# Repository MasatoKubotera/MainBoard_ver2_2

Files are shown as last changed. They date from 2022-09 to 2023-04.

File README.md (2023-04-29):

<html lang="en">
  <head>
    <meta charset="uft-8">
    <meta name="author" content="Masato Kubotera">
  </head>
  <body>
    <h1>Main Board Ver. 2.2</h1>
    <h2>About Main Board</h2>
    <p>
      The Main Board is a single board that integrates the circuits for driving the robot designed to be mounted on SUSTAINA-OP.
      <br>
      <br>
      Note that this is Ver. 2.2. For other versions, please refer to the following repositories.
      <ul>
        <li><a href="https://github.com/MasatoKubotera/MainBoard_ver2_0">Main Board Ver. 2.0</a></li>
        <li><a href="https://github.com/MasatoKubotera/MainBoard_ver2_1">Main Board Ver. 2.1</a></li>
      </ul>
      <h2>About Ver. 2.2</h2>
      now writing...
      <br><br>
      It is actually used for the 6th generation robot SUSTAINA-OP of the RoboCup Humanoid League team CIT Brains competed in the RoboCup 2022.<br><br>
      <!--
      -->
      <table>
        <tr>
          <td>
            <a href="image/brd_top.png">
              <div align="center">
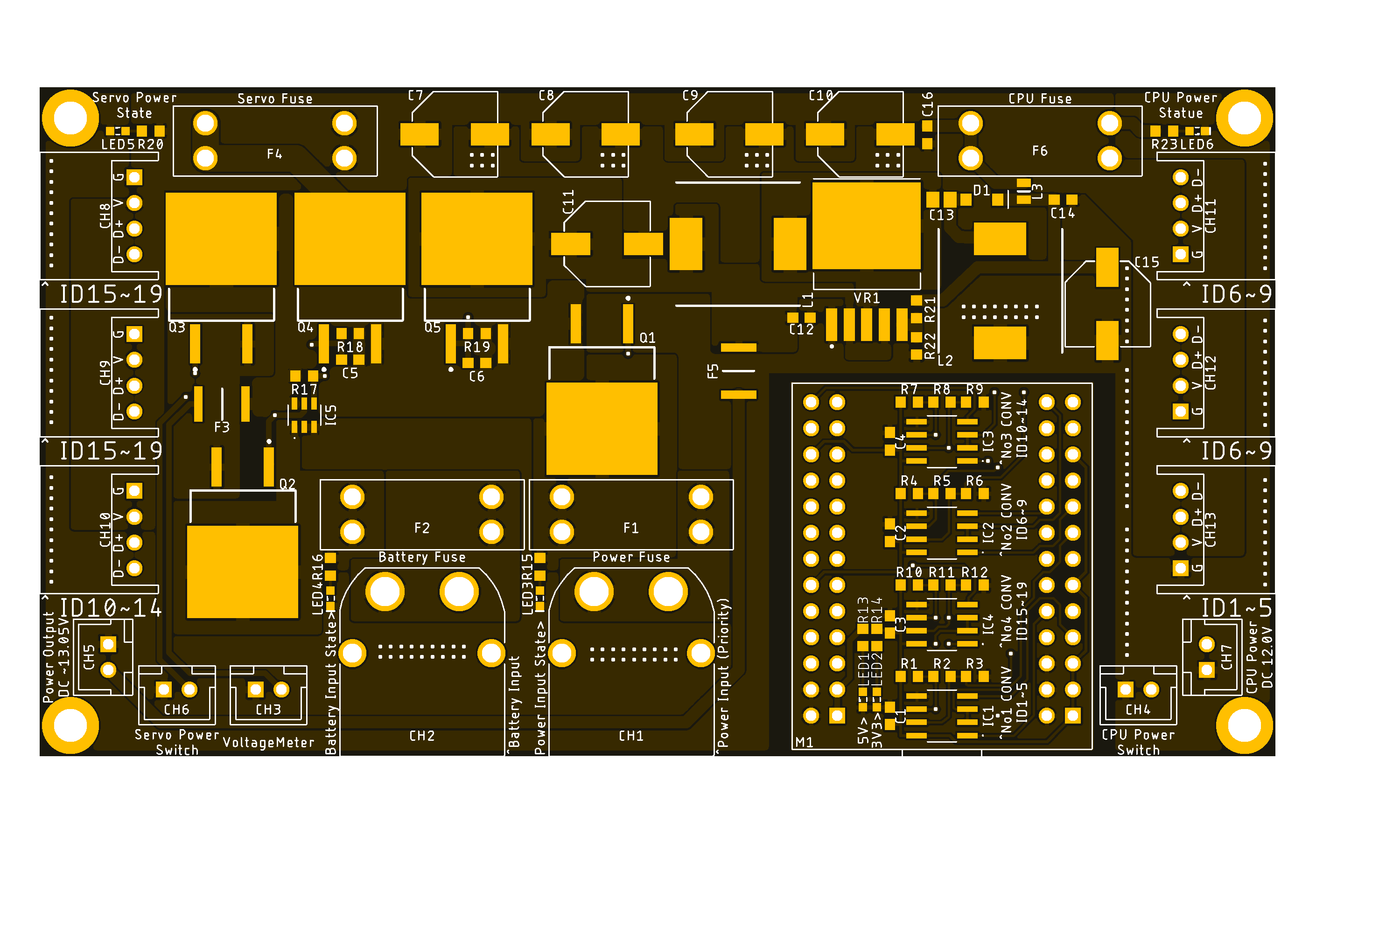
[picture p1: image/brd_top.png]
                
              </div>
            </a>
          </td>
          <td>
            <div align="center">
              
            </div>
          </td>
          <td>
            <div align="center">
              
            </div>
          </td>
        </tr>
        <tr>
          <td>
            <div align="center">
              PCB preview image
            </div>
          </td>
          <td>
            <div align="center">
              After mounting electronic components
            </div>
          </td>
          <td>
            <div align="center">
              After attaching module board
            </div>
          </td>     
        </tr>
      </table>
    </p>
    <h2>Repository Contents</h2>
    <p>
    <dl>
      <dt>\image</dt>
      <dd>PCB preview images and capture of design screen</dd>
      <dt>\libraries</dt>
      <dd>Libraries used in Autodesk Eagle design</dd>
      <dt>Schematic.pdf</dt>
      <dd>Circuit diagram of this product</dd>
      <dt>BOM.txt</dt>
      <dd>Parts lists output from design data</dd>
      <dt>.brd</dt>
      <dd>Board wiring design file by Autodesk Eagle</dd>
      <dt>.sch</dt>
      <dd>Schematic design file by Autodesk Eagle</dd>
      <dt>Gerber_data.zip</dt>
      <dd>Zip folder of Gerber format files for PCB manufacturing requests.</dd>
      <dt>LICENSE</dt>
      <dd>This is a license to use this product. Please confirm before use.</dd>
      <dt>.gitignore</dt>
      <dd>File to exclude cache files from management.</dd>
    </dl>
    </p>
    <h2>Documentation</h2>
      <p>
        <h3>BOM</h3>
        The BOM below shows the components actually mounted on the SUSTAINA-OP equipped MainBoard in RoboCup2022. Many of these boards have been created, and in some cases substitutes have been used. Their details are listed below the BOM.
          <table>
            <thead>
              <tr>
                <th> Eagle Design Parts # </th>
                <th> Q'ty </th>
                <th> Mfr. Product # </th>
                <th> Supplier </th>
                <th> Description </th>
              </tr>
            </thead>
            <tbody>
              <tr>
                <td>C1, C2, C3, C4, C5, C6</td>
                <td>6</td>
                <td>C1608JB1H104K</td>
                <td><a href="https://akizukidenshi.com/catalog/g/gP-06166/">Akizuki</a></td>
                <td>Multilayer Ceramic Capacitors SMD/SMT 0.1uF 50V 10% 0603</td>
              </tr>
              <tr>
                <td>C11,C15</td>
                <td>2</td>
                <td>UWT1E221MNL1GS</td>
                <td><a href="https://akizukidenshi.com/catalog/g/gP-10420/">Akizuki</a></td>
                <td>Aluminum Electrolytic Capacitors SMD/SMT 220uF 25V 20% AEC-Q200</td>
              </tr>
              <tr>
                <td>C12,C14</td>
                <td>2</td>
                <td>GRM188R71E105KA12</td>
                <td><a href="https://akizukidenshi.com/catalog/g/gP-14526/">Akizuki</a></td>
                <td>Multilayer Ceramic Capacitors SMD/SMT 1uF 25V 10% 0603</td>
              </tr>
              <tr>
                <td>C13</td>
                <td>1</td>
                <td>GRM21BR61E226ME44</td>
                <td><a href="https://akizukidenshi.com/catalog/g/gP-08240/">Akizuki</a></td>
                <td>Multilayer Ceramic Capacitors SMD/SMT 22uF 25V 15% 0603</td>
              </tr>
              <tr>
                <td>C16</td>
                <td>1</td>
                <td>GRM188R6YA106MA73</td>
                <td><a href="https://akizukidenshi.com/catalog/g/gP-13161/">Akizuki</a></td>
                <td>Multilayer Ceramic Capacitors SMD/SMT 10uF 35V 20% 0603</td>
              </tr>
              <tr>
                <td>C7, C8, C9, C10</td>
                <td>4</td>
                <td>35PFV150M8X10.5</td>
                <td><a href="https://akizukidenshi.com/catalog/g/gP-14492/">Akizuki</a></td>
                <td>Aluminum Organic Polymer Capacitors SMD/SMT 150uF 35V 20% AEC-Q200</td>
              </tr>
              <tr>
                <td>CH1, CH2</td>
                <td>2</td>
                <td>XT60PW-M</td>
                <td><a href="https://store.shopping.yahoo.co.jp/suzakulab/amass-xt60pw-m.html">Suzaku Lab.</a></td>
                <td>DC Power Connector, Through Hole, Horizontal, Male, 30A 500V</td>
              </tr>
              <tr>
                <td>CH3</td>
                <td>1</td>
                <td>B2B-XH-A-BLACK</td>
                <td><a href="https://www.daisen-netstore.com/shopdetail/000000000029/ct15/page1/order/">DAISEN</a></td>
                <td>Connector Header Through Hole, Top entry 2 position 2.54mm BLACK</td>
              </tr>
              <tr>
                <td>CH4</td>
                <td>1</td>
                <td>B2B-XH-A-BLUE</td>
                <td><a href="https://www.daisen-netstore.com/shopdetail/000000000029/ct15/page1/order/">DAISEN</a></td>
                <td>Connector Header Through Hole, Top entry 2 position 2.54mm BLUE</td>
              </tr>
              <tr>
                <td>CH5</td>
                <td>1</td>
                <td>B2B-XH-A-GREEN</td>
                <td><a href="https://www.daisen-netstore.com/shopdetail/000000000029/ct15/page1/order/">DAISEN</a></td>
                <td>Connector Header Through Hole, Top entry 2 position 2.54mm GREEN</td>
              </tr>
              <tr>
                <td>CH6</td>
                <td>1</td>
                <td>B2B-XH-A-YELLOW</td>
                <td><a href="https://www.daisen-netstore.com/shopdetail/000000000029/ct15/page1/order/">DAISEN</a></td>
                <td>Connector Header Through Hole, Top entry 2 position 2.54mm YELLOW</td>
              </tr>
              <tr>
                <td>CH7</td>
                <td>1</td>
                <td>B2B-XH-A-RED</td>
                <td><a href="https://www.daisen-netstore.com/shopdetail/000000000029/ct15/page1/order/">DAISEN</a></td>
                <td>Connector Header Through Hole, Top entry 2 position 2.54mm RED</td>
              </tr>
              <tr>
                <td>CH8, CH9</td>
                <td>2</td>
                <td>S4B-XH-A(LF)(SN)-YELLOW</td>
                <td><a href="https://www.daisen-netstore.com/shopdetail/000000000028/ct15/page1/order/">DAISEN</a></td>
                <td>Connector Header Through Hole, Side entry 4 position 2.54mm YELLOW</td>
              </tr>
              <tr>
                <td>CH10</td>
                <td>1</td>
                <td>S4B-XH-A(LF)(SN)-GREEN</td>
                <td><a href="https://www.daisen-netstore.com/shopdetail/000000000028/ct15/page1/order/">DAISEN</a></td>
                <td>Connector Header Through Hole, Side entry 4 position 2.54mm GREEN</td>
              </tr>
              <tr>
                <td>CH11, CH12</td>
                <td>2</td>
                <td>S4B-XH-A(LF)(SN)-BLUE</td>
                <td><a href="https://www.daisen-netstore.com/shopdetail/000000000028/ct15/page1/order/">DAISEN</a></td>
                <td>Connector Header Through Hole, Side entry 4 position 2.54mm BLUE</td>
              </tr>
              <tr>
                <td>CH13</td>
                <td>1</td>
                <td>S4B-XH-A(LF)(SN)-RED</td>
                <td><a href="https://www.daisen-netstore.com/shopdetail/000000000028/ct15/page1/order/">DAISEN</a></td>
                <td>Connector Header Through Hole, Side entry 4 position 2.54mm RED</td>
              </tr>
              <tr>
                <td>D1</td>
                <td>1</td>
                <td>SS34FA</td>
                <td><a href="https://www.mouser.jp/ProductDetail/512-SS34FA">Mouser</a></a></td>
                <td>Schottky Barrier Rectifiers SMD/SMT 3 A 40 V</td>
              </tr>
              <tr>
                <td>F1, F2, F4</td>
                <td>3</td>
                <td>0891020.NXS</td>
                <td><a href="https://www.mouser.jp/ProductDetail/576-0891020.NXS">Mouser</a></td>
                <td>Automotive Fuses LP MINI 58V 20A</td>
              </tr>
              <tr>
                <td>F1, F2, F4, F6</td>
                <td>4</td>
                <td>3557-2</td>
                <td><a href="https://www.mouser.jp/ProductDetail/534-3557-2">Mouser</a></td>
                <td>Fuse Holder Through Hole 500V 30A</td>
              </tr>
              <tr>
                <td>F3</td>
                <td>1</td>
                <td>MF-MSMF010</td>
                <td><a href="https://akizukidenshi.com/catalog/g/gP-15428/">Akizuki</a></td>
                <td>PTC Resettable Fuses SMD/SMT 0.1A 60V 1812</td>
              </tr>
              <tr>
                <td>F5</td>
                <td>1</td>
                <td>MF-MSMF050/30X-2</td>
                <td><a href="https://www.mouser.jp/ProductDetail/652-MF-MSMF050/30X-2">Mouser</a></td>
                <td>PTC Resettable Fuses SMD/SMT 0.5A 30V 1812</td>
              </tr>
              <tr>
                <td>F6</td>
                <td>1</td>
                <td>MO-29</td>
                <td><a href="https://www.amazon.co.jp/dp/B0722VT9DQ/">Amazon</a></td>
                <td>Automotive Fuses LP MINI 7.5A</td>
              </tr>
              <tr>
                <td>IC1, IC2, IC3, IC4</td>
                <td>4</td>
                <td>ADM3078EARZ</td>
                <td><a href="https://www.mouser.jp/ProductDetail/584-ADM3078EARZ">Mouser</a></td>
                <td>3.3 V, ±15 kV ESD-Protected, Half- and Full-Duplex, RS-485/RS-422 Transceivers</td>
              </tr>
              <tr>
                <td>IC5</td>
                <td>1</td>
                <td>LTC4412ES6</td>
                <td><a href="https://akizukidenshi.com/catalog/g/gI-07305/">Akizuki</a></td>
                <td>PMIC Low Loss PowerPath Controller</td>
              </tr>
              <tr>
                <td>L1,L2</td>
                <td>2</td>
                <td>CDRH127/LDNP-470MC</td>
                <td><a href="https://akizukidenshi.com/catalog/g/gP-13966/">Akizuki</a></td>
                <td>Power Inductors - SMD 47uH 3.25A</td>
              </tr>
              <tr>
                <td>L3</td>
                <td>1</td>
                <td>DFE201210S-2R2M</td>
                <td><a href="https://akizukidenshi.com/catalog/g/gP-14976/">Akizuki</a></td>
                <td>Power Inductors - SMD 2.2 uH 1.5A</td>
              </tr>
              <tr>
                <td>LED1,LED2,LED3,LED4</td>
                <td>4</td>
                <td>150060VS86000</td>
                <td><a href="https://www.mouser.jp/ProductDetail/710-150060VS86000">Mouser</a></td>
                <td>Standard LEDs - SMD Green 2V 20mA 573nm 0603</td>
              </tr>
              <tr>
                <td>LED5,LED6</td>
                <td>2</td>
                <td>150060YS75000</td>
                <td><a href="https://www.mouser.jp/ProductDetail/710-150060YS75000">Mouser</a></td>
                <td>Standard LEDs - SMD Yellow 2V 20mA 590nm 0603</td>
              </tr>
              <tr>
                <td>M1</td>
                <td>1</td>
                <td>FT4232H MINI MODULE</td>
                <td><a href="https://www.mouser.jp/ProductDetail/895-FT4232HMINIMOD">Mouser</a></td>
                <td>Interface Development Tools USB Hi-Speed FT4323H Evaluation Module</td>
              </tr>
              <tr>
                <td>M1</td>
                <td>2</td>
                <td>FH-2x13SG</td>
                <td><a href="https://akizukidenshi.com/catalog/g/gC-00084/">Akizuki</a></td>
                <td>2.54mm Pin Socket, 2 Row, 26 Pin</td>
              </tr>
              <tr>
                <td>Q1, Q2, Q3, Q4, Q5</td>
                <td>5</td>
                <td>SQM40P10-40L_GE3</td>
                <td><a href="https://www.mouser.jp/ProductDetail/78-SQM40P10-40L_GE3">Mouser</a></td>
                <td>Pch MOSFET 100V 40A 150W 33mohm</td>
              </tr>
              <tr>
                <td>R1, R3, R4, R6, R7, R9, R10, R12</td>
                <td>8</td>
                <td>RC0603FR-10680RL</td>
                <td><a href="https://www.mouser.jp/ProductDetail/603-RC0603FR-10680RL">Mouser</a></td>
                <td>Thick Film Resistors - SMD 680 Ohms 100-200mW 1% 0603</td>
              </tr>
              <tr>
                <td>R13, R14, R22</td>
                <td>3</td>
                <td>RC0603FR-101KL</td>
                <td><a href="https://www.mouser.jp/ProductDetail/603-RC0603FR-101KL">Mouser</a></td>
                <td>Thick Film Resistors - SMD 1 kOhms 100-200mW 1% 0603</td>
              </tr>
              <tr>
                <td>R15, R16, R20, R23</td>
                <td>4</td>
                <td>RC0603FR-102KL</td>
                <td><a href="https://www.mouser.jp/ProductDetail/603-RC0603FR-102KL">Mouser</a></td>
                <td>Thick Film Resistors - SMD 2 kOhms 100-200mW 1% 0603</td>
              </tr>
              <tr>
                <td>R17</td>
                <td>1</td>
                <td>RC0603FR-10470KL</td>
                <td><a href="https://www.mouser.jp/ProductDetail/603-RC0603FR-10470KL">Mouser</a></td>
                <td>Thick Film Resistors - SMD 470 kOhms 100-200mW 1% 0603</td>
              </tr>
              <tr>
                <td>R21</td>
                <td>1</td>
                <td>RC0603FR-078K66L</td>
                <td><a href="https://www.mouser.jp/ProductDetail/603-RC0603FR-078K66L">Mouser</a></td>
                <td>Thick Film Resistors - SMD 8.66 kOhms 100-200mW 1% 0603</td>
              </tr>
              <tr>
                <td>R18, R19</td>
                <td>2</td>
                <td>RC0603FR-1010KL</td>
                <td><a href="https://www.mouser.jp/ProductDetail/603-RC0603FR-1010KL">Mouser</a></td>
                <td>Thick Film Resistors - SMD 10 kOhms 100-200mW 1% 0603</td>
              </tr>
              <tr>
                <td>R2, R5, R8, R11</td>
                <td>4</td>
                <td>RC0603FR-10120RL</td>
                <td><a href="https://www.mouser.jp/ProductDetail/603-RC0603FR-10120RL">Mouser</a></td>
                <td>Thick Film Resistors - SMD 120 Ohms 100-200mW 1% 0603</td>
              </tr>
              <tr>
                <td>VR1</td>
                <td>1</td>
                <td>XL6009E1</td>
                <td><a href="https://www.aitendo.com/product/10307">Aitendo</a></td>
                <td>400KHz 60V 4A Switching Current Boost / Buck-Boost / Inverting DC/DC Converter</td>
              </tr>
            </tbody>
          </table>
          <details>
            <summary>Substitutes</summary>
            Used for No. 1 ~ No. 7
            <table>
              <thead>
                <tr>
                  <th> Eagle Design Parts # </th>
                  <th> Q'ty </th>
                  <th> Mfr. Product # </th>
                  <th> Supplier </th>
                  <th> Description </th>
                </tr>
              </thead>
              <tbody>
                <tr>
                  <td>C1, C2, C3, C4, C5, C6</td>
                  <td>6</td>
                  <td>GCM188L81H104K57</td>
                  <td><a href="https://akizukidenshi.com/catalog/g/gP-16143/">Akizuki</a></td>
                  <td>Multilayer Ceramic Capacitors SMD/SMT 0.1uF 50V 10% 0603</td>
                </tr>
              </tbody>
            </table>
            Used for No. 13 ~ 
            <table>
              <thead>
                <tr>
                  <th> Eagle Design Parts # </th>
                  <th> Q'ty </th>
                  <th> Mfr. Product # </th>
                  <th> Supplier </th>
                  <th> Description </th>
                </tr>
              </thead>
              <tbody>
                <tr>
                  <td>Q1, Q2, Q3, Q4, Q5</td>
                  <td>5</td>
                  <td>SUM110P06-08L-E3</td>
                  <td><a href="https://www.mouser.jp/ProductDetail/781-SUM110P06-08L-E3">Mouser</a></td>
                  <td>Pch MOSFET 60V 110A 272W 8.0mohm</td>
                </tr>
              </tbody>
            </table>
          </details>  
        <h3>PCB Fabrication</h3>
          PCB(Printed Circuit Board) manufacturing was outsourced to <a href="https://www.elecrow.com/pcb-manufacturing.html">Elecrow</a>.<br>
          The custom specifications are as follows.
          <ul>
            <li>Layer : 2 layers</li>
            <li>Dimensions : 120 x 65</li>
            <li>Different PCB Design : 1eg</li>
            <li>PCB Thickness : 1.6</li>
            <li>PCB Color : Black</li>
            <li>Surface Finish : HASL Lead Free</li>
            <li>Castellated Hole : No</li>
            <li>Copper Weight : 2oz</li>
            <li>PCB Stencil : Stencil 15cm X 15cm no frame</li>
            <li>Stencil Side : Top</li>
          </ul>
          The data used to order fabrication are as follows.
          <ul>
            <li>Eagle design rule : <a href="https://www.elecrow.com/download/Elecrow_PCB_eagle_rule.zip">Elecrow Eagle Design Rule</a></li>
            <li>Eagle CAM file : <a href="https://www.elecrow.com/download/Elecrow_Gerber_Generater_DrillAlign.zip">Elecrow CAM file</a></li>
            <li>Gerber format data : <a href="/Gerber_data.zip">Gerber_data.zip</a></li>
          </ul>
        <h3>Issues with this board</h3>
        <ul>
          <li>Heat generation problem of FETs</li>
          <li>Poor inrush current protection by load switch circuit</li>
        </ul>
        <h3>References</h3>
        <ul>
          <li> 4-Parallel Servo Motor Control with FT4232H MINI MODULE
            <ul>
              <li> <a href=""https://2019.robocup.org/downloads/program/BestmannEtAl2019.pdf">Bestmann, Marc & Güldenstein, Jasper & Zhang, Jianwei. (2019). High-Frequency Multi Bus Servo and Sensor Communication Using the Dynamixel Protocol. </a></li>
              <li> Wolfgang CORE : https://github.com/bit-bots/wolfgang_core</li>
             </ul>
          </li>
        </ul>
      </p>
    <h2>Contact</h2>
    <p>
    If you have any questions, please contact MasatoKubotera, the product's designer, by E-mail.<br>
    E-mail : <a href="mailto:masatokubotera06@yahoo.co.jp">masatokubotera06@yahoo.co.jp</a>
    </p>
    <h2>License Information</h2>
    <p>
      This product is open source.<br>
      Please review the <a href="/LICENSE">LICENSE file</a> for license information.<br>
      <br>
      <strong>Main Board Ver. 2.2</strong> by Masato Kubotera is licensed under a <a href="http://creativecommons.org/licenses/by-nc-sa/4.0/">Creative Commons Attribution-NonCommercial-ShareAlike 4.0 International License</a>.
    </p>    
  </body>
</html>

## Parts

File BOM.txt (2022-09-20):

Partlist exported from C:/Users/Masato/Documents/citbrains/MainBoard_ver2_2/MainBoard_ver2_2.sch at 2022/09/21 4:07

Qty Value               Device              Package             Parts                              Description                
6                       LEDSML0603          SML0603             LED1, LED2, LED3, LED4, LED5, LED6 LED                        
6   0.1u                C-USC0603           C0603               C1, C2, C3, C4, C5, C6             CAPACITOR, American symbol 
2   10k                 R-US_R0603          R0603               R18, R19                           RESISTOR, American symbol  
1   10u                 C-USC0603           C0603               C16                                CAPACITOR, American symbol 
4   120                 R-US_R0603          R0603               R2, R5, R8, R11                    RESISTOR, American symbol  
3   1k                  R-US_R0603          R0603               R13, R14, R22                      RESISTOR, American symbol  
2   1u                  C-USC0603           C0603               C12, C14                           CAPACITOR, American symbol 
1   22u                 C-USC2012           C2012               C13                                CAPACITOR, American symbol 
4   2k                  R-US_R0603          R0603               R15, R16, R20, R23                 RESISTOR, American symbol  
4   3557-2              3557-2              3557-2              F1, F2, F4, F6                                                
4   35PFV150M8X10.5     35PFV150M8X10.5     35PFV150M8X10.5     C7, C8, C9, C10                                               
1   470k                R-US_R0603          R0603               R17                                RESISTOR, American symbol  
8   680                 R-US_R0603          R0603               R1, R3, R4, R6, R7, R9, R10, R12   RESISTOR, American symbol  
1   8.66k               R-US_R0603          R0603               R21                                RESISTOR, American symbol  
4   ADM3078E            ADM3078E            ADM3078E            IC1, IC2, IC3, IC4                                            
5   B2B-XH-A            B2B-XH-A            B2B-XH-A            CH3, CH4, CH5, CH6, CH7                                       
2   CDRH127/LDNP-470MC  CDRH127/LDNP-470MC  CDRH127/LDNP        L1, L2                                                        
1   DFE201210S-2R2M     DFE201210S-2R2M     DFE201210S          L3                                                            
1   FT4232H_MINI_MODULE FT4232H_MINI_MODULE FT4232H_MINI_MODULE M1                                                            
1   LTC4412             LTC4412             LTC4412             IC5                                                           
1   MF-MSMF010          MF-MSMF010          MF-MSMF010          F3                                                            
1   MF-MSMF050/30X      MF-MSMF050/30X      MF-MSMF050          F5                                                            
6   S4B-XH-A            S4B-XH-A            S4B-XH-A            CH8, CH9, CH10, CH11, CH12, CH13                              
5   SQM40P10-40L_GE3    SQM40P10-40L_GE3    TO-252-3            Q1, Q2, Q3, Q4, Q5                                            
1   SS34FA              SS34FA              SS34FA              D1                                                            
2   UWT1E221MNL1GS      UWT1E221MNL1GS      UWT1E221MNL1GS      C11, C15                                                      
1   XL6009E1            XL6009E1            TO263-5L            VR1                                                           
2   XT60PW-M            XT60PW-M            XT60PW-M            CH1, CH2

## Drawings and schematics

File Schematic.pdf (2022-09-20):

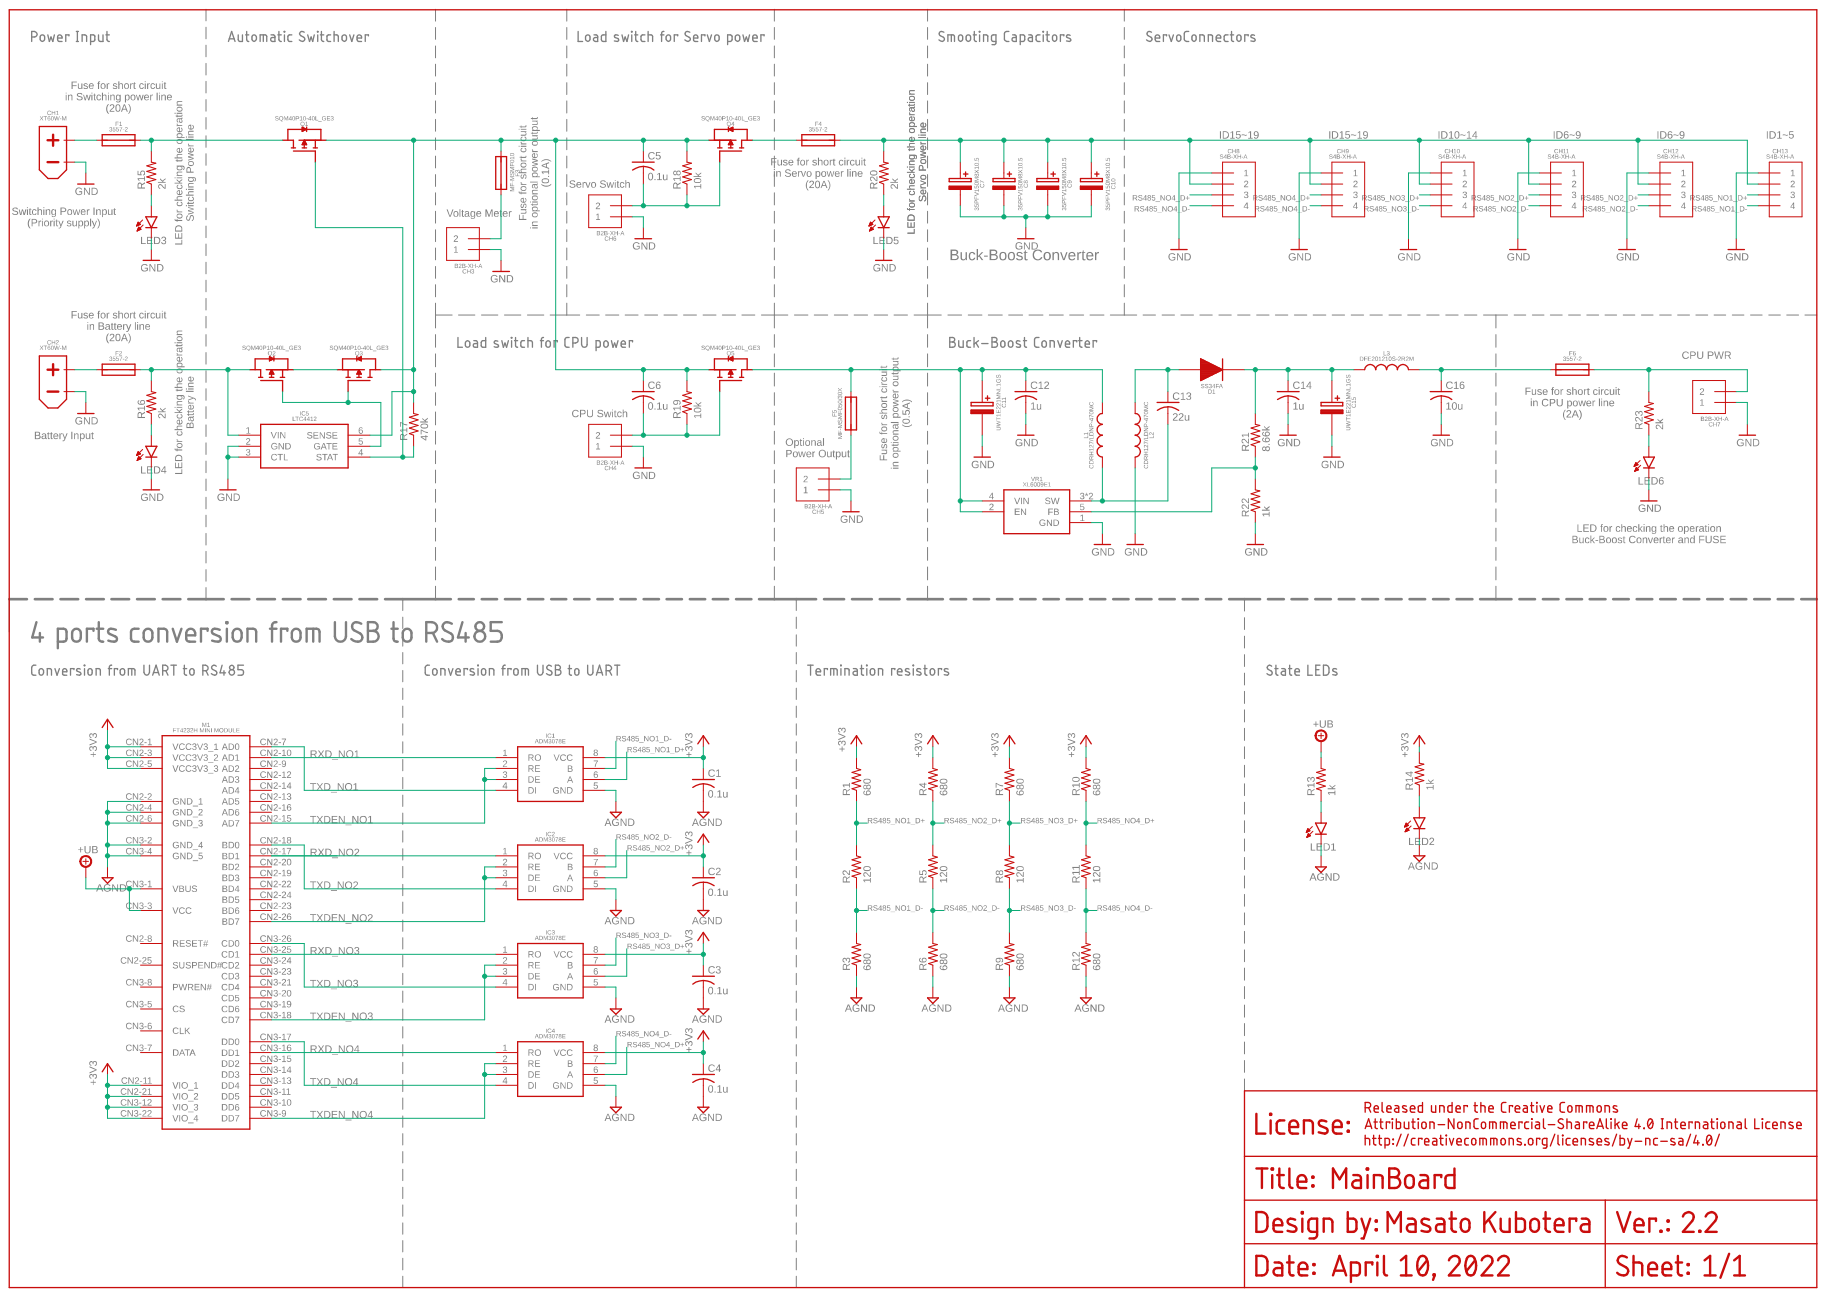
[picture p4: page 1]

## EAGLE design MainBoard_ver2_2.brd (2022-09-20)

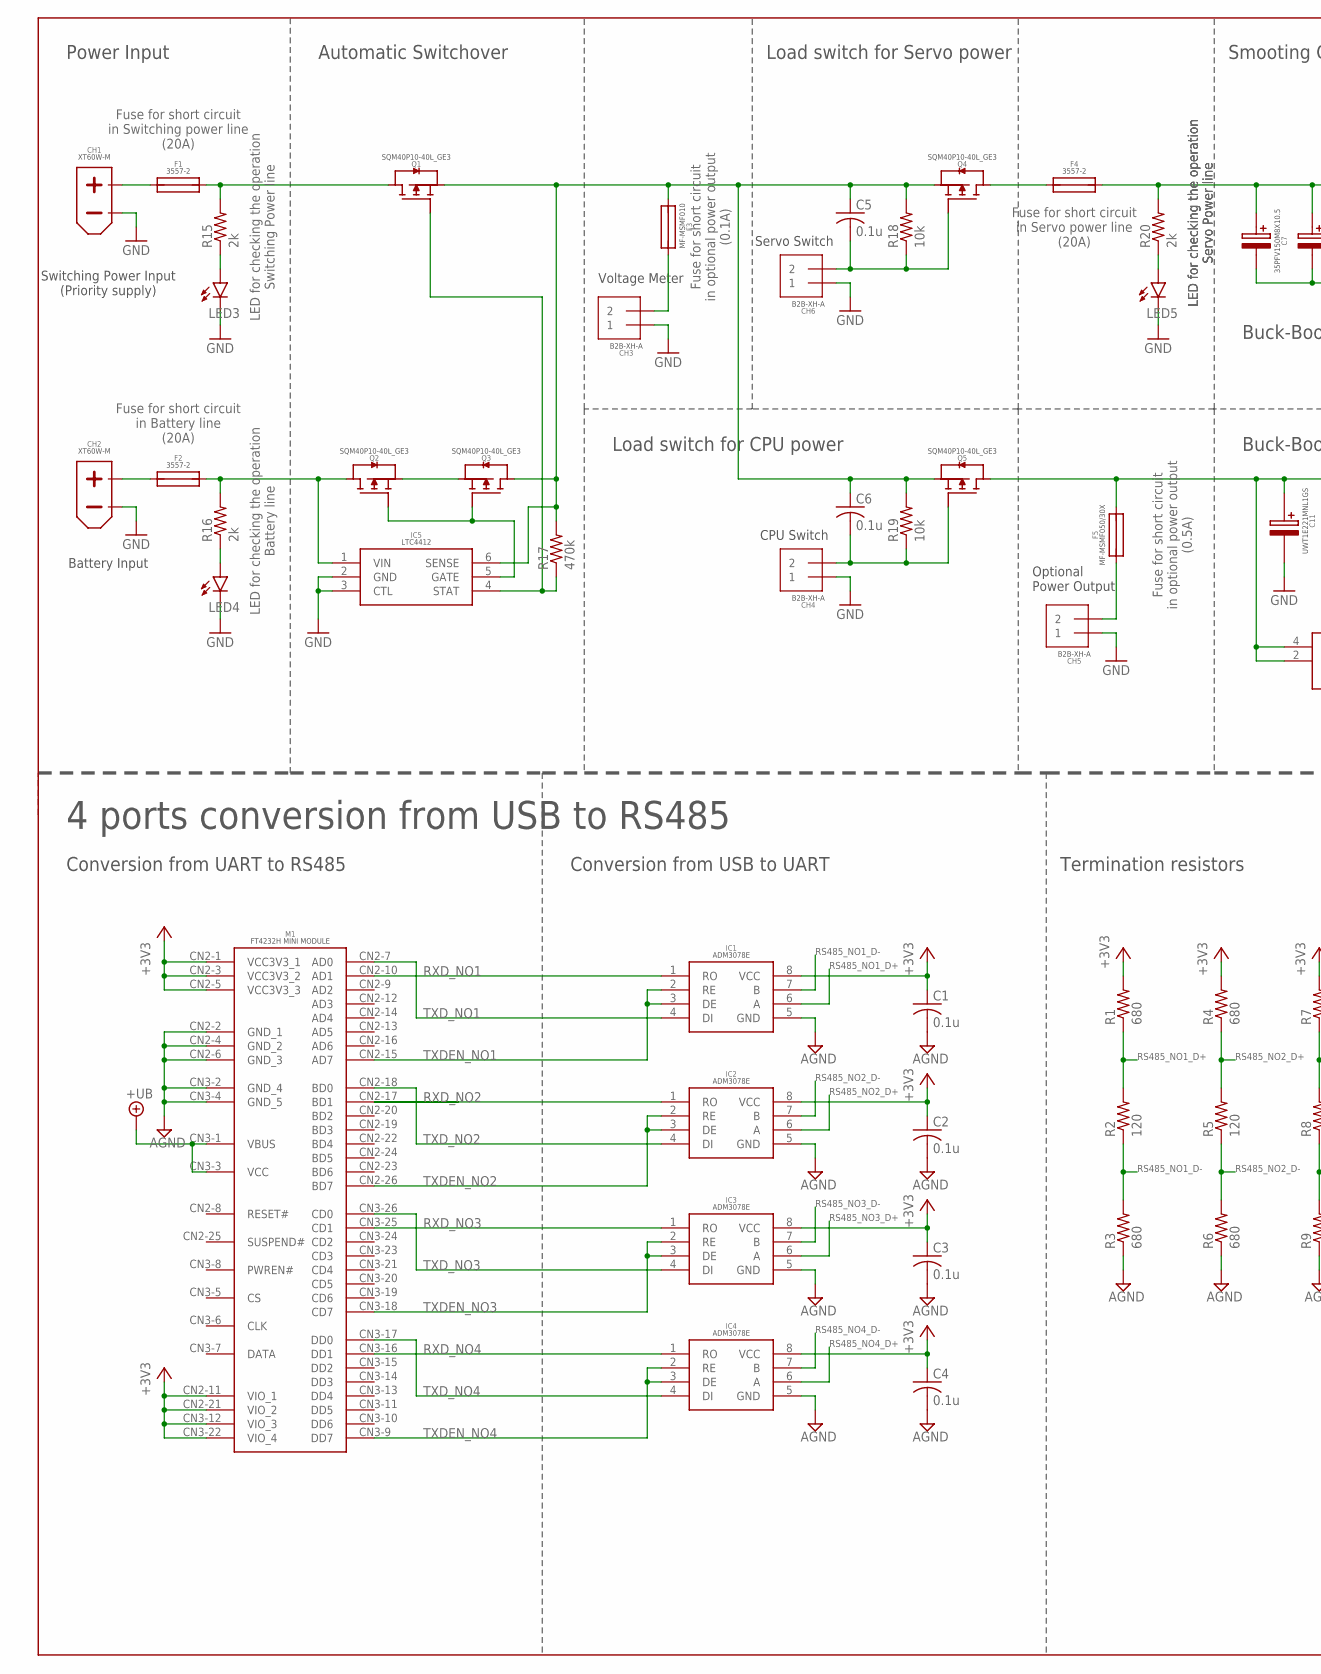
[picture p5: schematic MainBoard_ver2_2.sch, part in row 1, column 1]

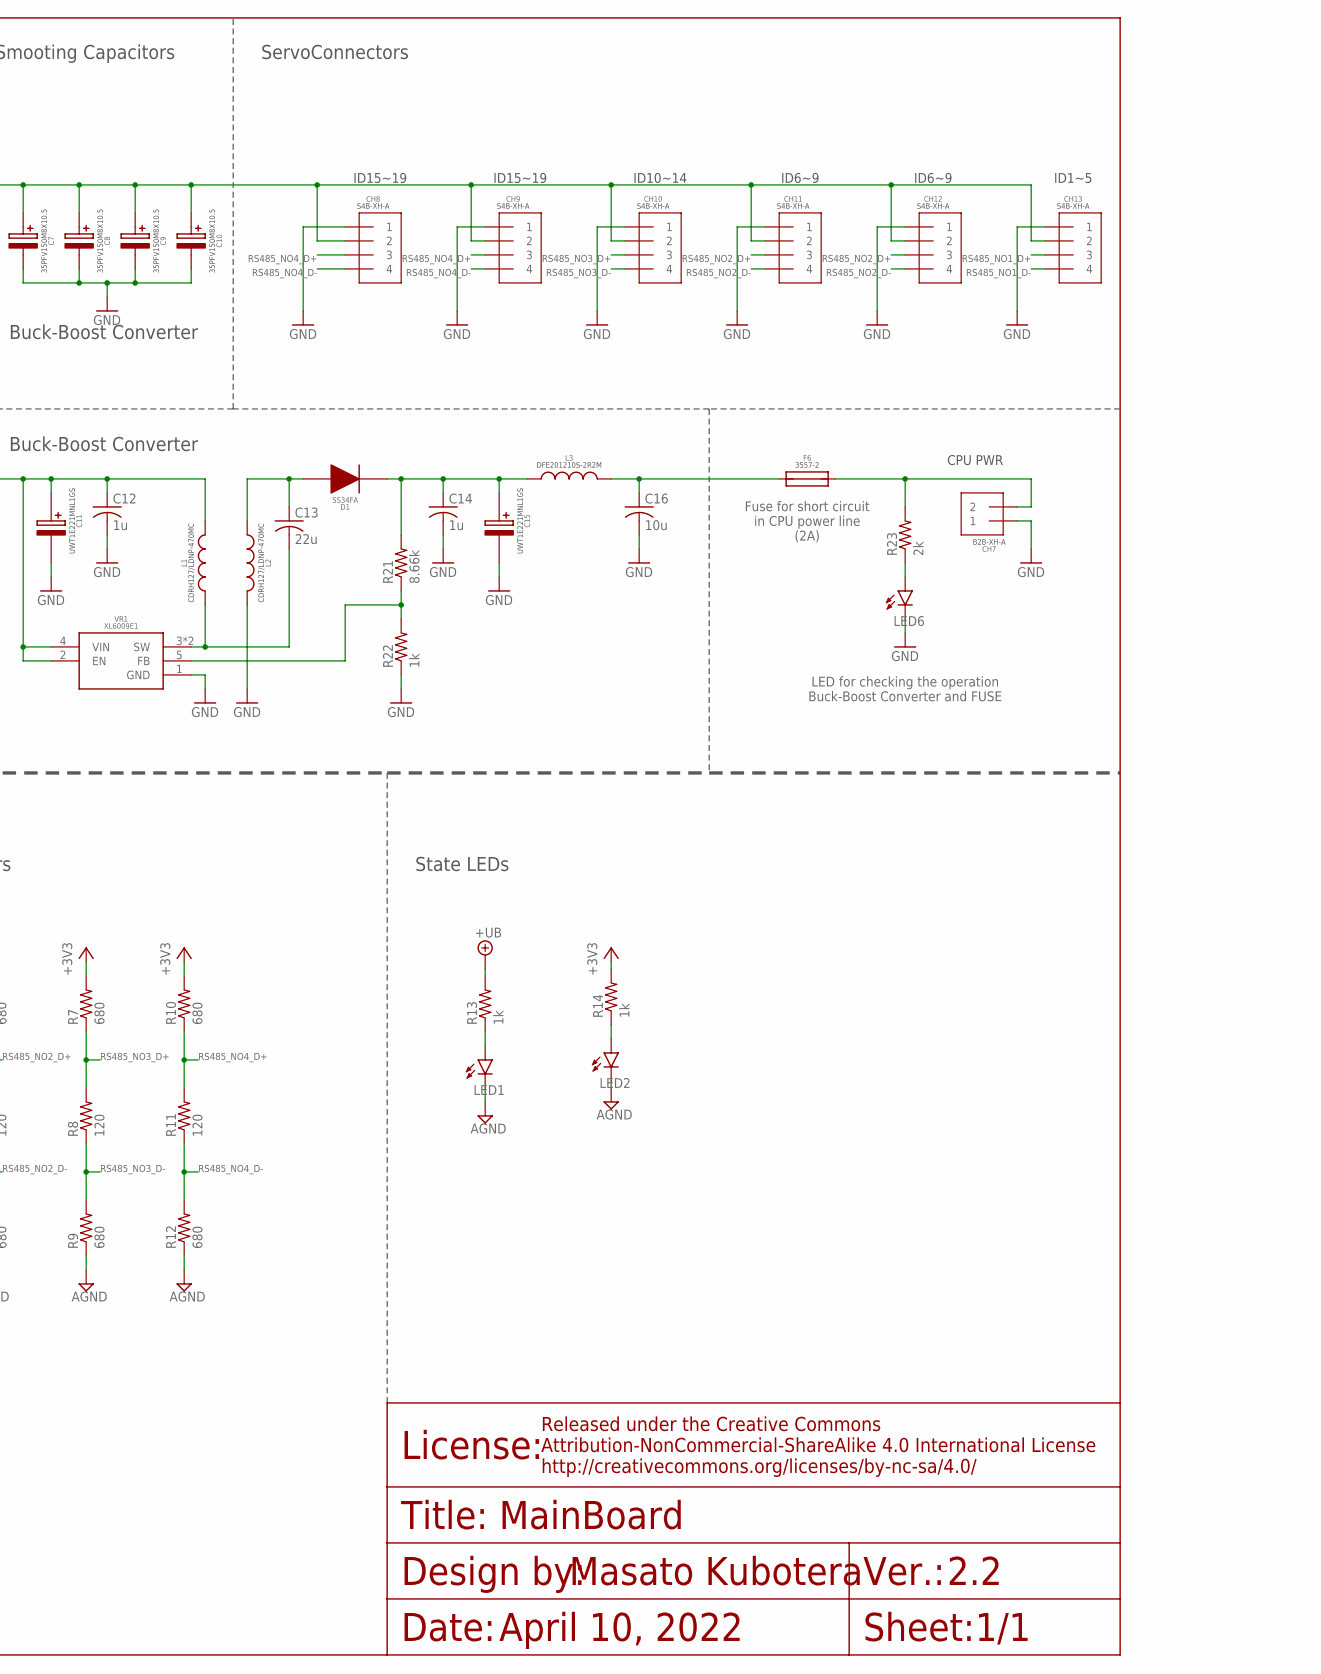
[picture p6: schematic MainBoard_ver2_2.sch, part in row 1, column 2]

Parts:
C1, C2, C3, C4, C5, C6: 0.1u; C0603
C7, C8, C9, C10: 35PFV150M8X10.5
C11, C15: UWT1E221MNL1GS
C12, C14: 1u; C0603
C13: 22u; C2012
C16: 10u; C0603
CH1, CH2: XT60PW-M
CH3, CH4, CH5, CH6, CH7: B2B-XH-A
CH8, CH9, CH10, CH11, CH12, CH13: S4B-XH-A
D1: SS34FA
F1, F2, F4, F6: 3557-2
F3: MF-MSMF010
F5: MF-MSMF050/30X; MF-MSMF050
IC1, IC2, IC3, IC4: ADM3078E
IC5: LTC4412
L1, L2: CDRH127/LDNP-470MC; CDRH127/LDNP
L3: DFE201210S-2R2M; DFE201210S
LED1, LED2, LED3, LED4, LED5, LED6: LEDSML0603; SML0603
M1: FT4232H_MINI_MODULE
Q1, Q2, Q3, Q4, Q5: SQM40P10-40L_GE3; TO-252-3
R1, R3, R4, R6, R7, R9, R10, R12: 680; R0603
R2, R5, R8, R11: 120; R0603
R13, R14, R22: 1k; R0603
R15, R16, R20, R23: 2k; R0603
R17: 470k; R0603
R18, R19: 10k; R0603
R21: 8.66k; R0603
VR1: XL6009E1; TO263-5L

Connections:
+3V3: C1.1, C2.1, C3.1, C4.1, IC1.8 (VCC), IC2.8 (VCC), IC3.8 (VCC), IC4.8 (VCC), M1.CN2-1 (VCC3V3_1), M1.CN2-3 (VCC3V3_2), M1.CN2-5 (VCC3V3_3), M1.CN2-11 (VIO_1), M1.CN2-21 (VIO_2), M1.CN3-12 (VIO_3), M1.CN3-22 (VIO_4), R1.2, R4.2, R7.2, R10.2, R14.2
+UB: M1.CN3-1 (VBUS), M1.CN3-3 (VCC), R13.2
AGND: C1.2, C2.2, C3.2, C4.2, IC1.5 (GND), IC2.5 (GND), IC3.5 (GND), IC4.5 (GND), LED1.C, LED2.C, M1.CN2-2 (GND_1), M1.CN2-4 (GND_2), M1.CN2-6 (GND_3), M1.CN3-2 (GND_4), M1.CN3-4 (GND_5), R3.1, R6.1, R9.1, R12.1
A_DIODE_DCDC: C14.1, C15.+, D1.1, L3.1, R21.2
A_FUSE_BATT: F2.3 (2), F2.4 (2), IC5.1 (VIN), Q2.4 (D), R16.2
A_FUSE_DCDC: CH7.2, F6.3 (2), F6.4 (2), R23.2
A_FUSE_METER: CH3.2, F3.2
A_FUSE_PWR: F1.3 (2), F1.4 (2), Q1.4 (D), R15.2
A_FUSE_SERVO: C7.+, C8.+, C9.+, C10.+, CH8.2, CH9.2, CH10.2, CH11.2, CH12.2, CH13.2, F4.3 (2), F4.4 (2), R20.2
B_DIODE_DCDC: C13.1, D1.2, L2.1
B_FUSE_BATT: CH2.+, F2.1, F2.2 (1)
B_FUSE_DCDC: C16.1, F6.1, F6.2 (1), L3.2
B_FUSE_PWR: CH1.+, F1.1, F1.2 (1)
B_FUSE_SERVO: F4.1, F4.2 (1), Q4.4 (D)
B_LOAD_CPU: C6.2, CH4.2, Q5.1 (G), R19.1
B_LOAD_SERVO: C5.2, CH6.2, Q4.1 (G), R18.1
CPU_PWR_IN: C11.+, C12.1, F5.2, L1.2, Q5.4 (D), VR1.2 (EN), VR1.4 (VIN)
FB_DCDC: R21.1, R22.2, VR1.5 (FB)
GND: C7.-, C8.-, C9.-, C10.-, C11.-, C12.2, C14.2, C15.-, C16.2, CH1.-, CH2.-, CH3.1, CH4.1, CH5.1, CH6.1, CH7.1, CH8.1, CH9.1, CH10.1, CH11.1, CH12.1, CH13.1, IC5.2 (GND), IC5.3 (CTL), L2.2, LED3.C, LED4.C, LED5.C, LED6.C, R22.1, VR1.1 (GND)
INPUT_PWR: C5.1, C6.1, F3.1, IC5.6 (SENSE), Q1.3 (S), Q3.4 (D), Q4.3 (S), Q5.3 (S), R17.2, R18.2, R19.2
LED_3V3: LED2.A, R14.1
LED_BATT: LED4.A, R16.1
LED_DCDCOUT: LED6.A, R23.1
LED_PWR: LED3.A, R15.1
LED_SERVO: LED5.A, R20.1
LED_UB: LED1.A, R13.1
LTC4412_GATE: IC5.5 (GATE), Q2.1 (G), Q3.1 (G)
LTC4412_STAT: IC5.4 (STAT), Q1.1 (G), R17.1
POWER_OUTPUT: CH5.2, F5.1
RS485_NO1_D+: CH13.3, IC1.6 (A), R1.1, R2.2
RS485_NO1_D-: CH13.4, IC1.7 (B), R2.1, R3.2
RS485_NO2_D+: CH11.3, CH12.3, IC2.6 (A), R4.1, R5.2
RS485_NO2_D-: CH11.4, CH12.4, IC2.7 (B), R5.1, R6.2
RS485_NO3_D+: CH10.3, IC3.6 (A), R7.1, R8.2
RS485_NO3_D-: CH10.4, IC3.7 (B), R8.1, R9.2
RS485_NO4_D+: CH8.3, CH9.3, IC4.6 (A), R10.1, R11.2
RS485_NO4_D-: CH8.4, CH9.4, IC4.7 (B), R11.1, R12.2
RXD_NO1: IC1.1 (RO), M1.CN2-10 (AD1)
RXD_NO2: IC2.1 (RO), M1.CN2-17 (BD1)
RXD_NO3: IC3.1 (RO), M1.CN3-25 (CD1)
RXD_NO4: IC4.1 (RO), M1.CN3-16 (DD1)
SOURCE: Q2.3 (S), Q3.3 (S)
SW_DCDC: C13.2, L1.1, VR1.3 (SW), VR1.6 (SW)
TXDEN_NO1: IC1.2 (RE), IC1.3 (DE), M1.CN2-15 (AD7)
TXDEN_NO2: IC2.2 (RE), IC2.3 (DE), M1.CN2-26 (BD7)
TXDEN_NO3: IC3.2 (RE), IC3.3 (DE), M1.CN3-18 (CD7)
TXDEN_NO4: IC4.2 (RE), IC4.3 (DE), M1.CN3-9 (DD7)
TXD_NO1: IC1.4 (DI), M1.CN2-7 (AD0)
TXD_NO2: IC2.4 (DI), M1.CN2-18 (BD0)
TXD_NO3: IC3.4 (DI), M1.CN3-26 (CD0)
TXD_NO4: IC4.4 (DI), M1.CN3-17 (DD0)

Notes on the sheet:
CPU Switch
Battery Input
Switching Power Input (Priority supply)
Servo Switch
Voltage Meter
Optional Power Output
ServoConnectors
Buck-Boost Converter
Smooting Capacitors
LED for checking the operation Buck-Boost Converter and FUSE
Fuse for short circuit in CPU power line (2A)
CPU PWR
Fuse for short circuit in Servo power line (20A)
Load switch for Servo power
Load switch for CPU power
Fuse for short circuit in optional power output (0.5A)
Automatic Switchover
Fuse for short circuit in Switching power line (20A)
Fuse for short circuit in Battery line (20A)
LED for checking the operation Switching Power line
LED for checking the operation Battery line
Fuse for short circuit in optional power output (0.1A)
LED for checking the operation Servo Power line
ID1~5
ID6~9
ID10~14
ID15~19
4 ports conversion from USB to RS485
Conversion from USB to UART
Termination resistors
State LEDs
2.2
1/1
April 10, 2022
MainBoard
Conversion from UART to RS485
Power Input

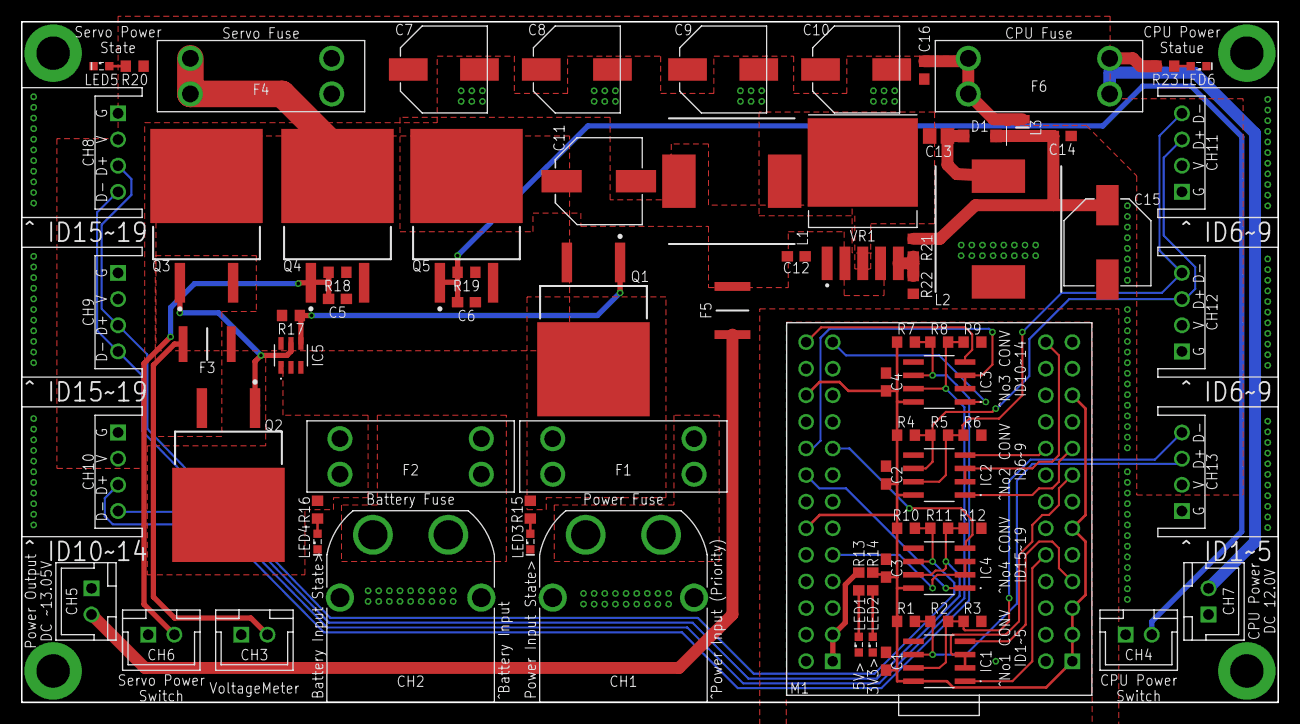
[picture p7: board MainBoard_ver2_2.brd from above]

Board: 2 copper layers, 120.0 x 65.0 mm, 80 parts (0 on the bottom side), 51 nets.

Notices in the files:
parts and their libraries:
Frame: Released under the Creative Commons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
